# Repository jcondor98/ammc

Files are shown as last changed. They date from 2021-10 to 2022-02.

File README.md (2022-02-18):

# Bachelor degree thesis

This branch contains the LaTeX source code and compiled PDFs for my bachelor
degree thesis and slides for the AVR Multi Motor Control project presentation.

**Relator**: Prof. Giorgio Grisetti
**Correlator**: Docs. Barbara Bazzana
**Evaluator**: Profs. Silvia Bonomi

The thesis is presented in the degree session of _March 2022_.

# Building

### Requirements
All the LaTeX source code in this branch can be compiled using the _GNU Make_
build system.

Building the thesis requires `xelatex` and `bibtex`.

Building the presentation slides requires `xelatex`.

A full _TeXLive_ installation is recommended.

### GNU Make recipes

**Command** | **Description**
:-:|---
`make thesis`       | Builds the thesis PDF with `xelatex`
`make bibliography` | Builds the bibliography with `bibtex`
`make slides`       | Builds the presentation slides with `xelatex`
`make`              | Alias for `make thesis`
`make clean`        | Removes all the build auxiliary files

For a complete thesis build (with correct references and bibliography), run the
following commands:

```
make thesis
make bibliography
make thesis
make thesis
```

### Target files
The thesis can be found under the main directory of this branch as `thesis.pdf`

The presentation slides can be found under the `presentation/` directory as
`slides.pdf`

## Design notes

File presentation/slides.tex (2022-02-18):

% AVR Multi Motor Control - Paolo Lucchesi
% Slides for project presentation
\documentclass{beamer}
\usepackage[T1]{fontenc}
\usepackage[utf8]{inputenc}
\usepackage{longtable,booktabs,array}
\usepackage{caption}
\usepackage{adjustbox}
\usepackage{palatino}

\newcommand*{\LimitedIncludeGraphics}[2][]{%
\begin{adjustbox}{max size={\textwidth}{\textheight}}
    %
\end{adjustbox}
}

\usetheme[]{Berlin}
\usecolortheme{beaver}
\beamertemplatenavigationsymbolsempty

\hypersetup{
  pdfauthor={Paolo Lucchesi},
  hidelinks
}

\title{AVR Multi Motor Control}
\author{Paolo Lucchesi}
\date{}

\begin{document}
\frame{\titlepage}

\hypertarget{introduction}{%
\section{Introduction}\label{introduction}}

\begin{frame}{What is ammc?}
\emph{AVR Multi Motor Control} is an electrical motor management
hardware/software ecosystem composed of:

\begin{itemize}
  \item A text-based \textbf{client} application
  \item One \textbf{master} controller
  \item One or more \textbf{slave} controllers
\end{itemize}
\end{frame}

\begin{frame}{Features}
\begin{itemize}
  \item Text-based client application for POSIX environments
  \item Master and Slave(s) controller firmware
  \item Fully binary Client-Master communication protocol on top of the serial
    interface
  \item Fully binary Master-Slave communication protocol on top of the I2C
    interface
  \item Up to 126 DC motors (limited by 7-bit I2C Slave addressing, 0x00 is
    reserved)
  \item Ability to get and set the DC motors speed, individually
  \item Software defined PID controller embedded in each Slave controller
\end{itemize}
\end{frame}

\begin{frame}{Development}
\begin{itemize}
  \item Focus on \textbf{modularity}
  \item Keeping \emph{SOLID} principles in mind
  \begin{itemize}
    \item Extensibility through the Open-Close Principle
    \item Attention on module call directions following the Single
      Responsability Principle
  \end{itemize}
  \item Exhaustive \textbf{documentation} on multiple depths
  \begin{itemize}
    \item README.md file in the git repository
    \item Source code documentation generated with \emph{doxygen}
    \item Client application's man page
    \item Bachelor degree thesis
  \end{itemize}
  \item GNU Make build system
  \item Absence of third-party non-standard libraries
\end{itemize}
\end{frame}

\hypertarget{client-application}{%
\section{Client Application}\label{client-application}}

\begin{frame}{Features}
\begin{itemize}
  \item Granular handling for getting and setting motors' speed
  \item Terminal User Interface implemented as a command shell
  \item Support for non-interactive use (i.e.~scripting)
  \item Communication with master controller using the serial protocol
  \item Compatible with POSIX-compliant environments
  \item Comes with a man page
\end{itemize}
\end{frame}

\begin{frame}{Software modules}
\begin{figure}
  \centering
  \LimitedIncludeGraphics{../source/images/client-deps.png}
  \caption{Client application modules dependency graph}
\end{figure}
\end{frame}

\begin{frame}{User Interface}
External commands allow to interface the master controller:

\begin{itemize}
  \item \texttt{connect\ \textless{}device-path\textgreater{}}
  \item \texttt{ping\ \textless{}motor-id\textgreater{}}
  \item \texttt{get-speed\ \textless{}motor-id\textgreater{}}
  \item \texttt{set-speed\ \textless{}motor-id\textgreater{}=\textless{}speed\textgreater{}}
  \item \texttt{apply}
  \item \texttt{set-slave-addr}
\end{itemize}
\end{frame}

\hypertarget{master-controller}{%
\section{Master Controller}\label{master-controller}}

\begin{frame}{Features}
\begin{itemize}
  \item Is itself an \textbf{ATMega2560} microcontroller unit
  \item Interfaces the client applications with the slave controllers
  \item Communicates with the client via serial
  \item Communicates with slaves via I2C
  \item Interrupt-driven communication
  \item Comes with a power saving policy
\end{itemize}
\end{frame}

\begin{frame}{Hardware setup}
\begin{figure}
  \centering
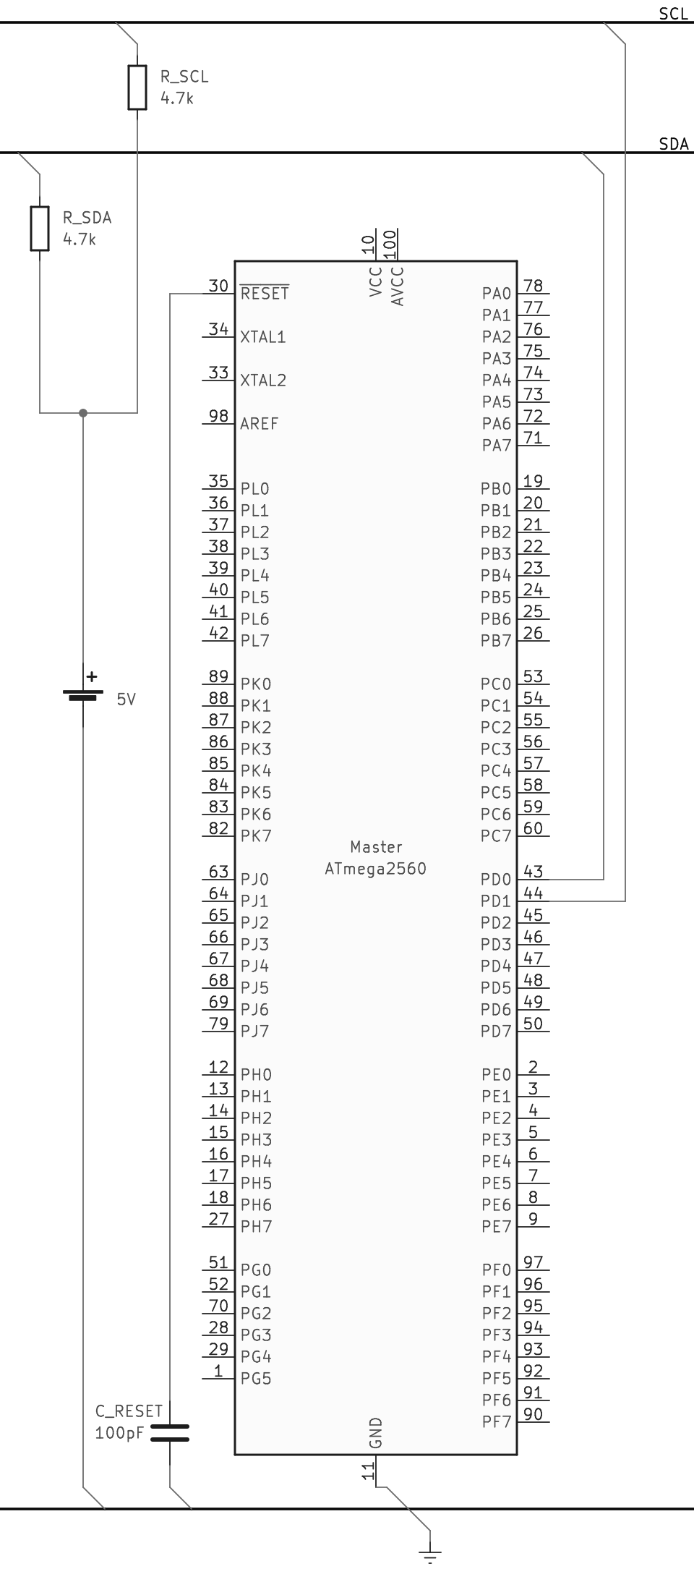
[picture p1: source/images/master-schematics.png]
  
  \caption{Master controller schematics}
\end{figure}
\end{frame}

\begin{frame}{Software modules}
\begin{figure}
  \centering
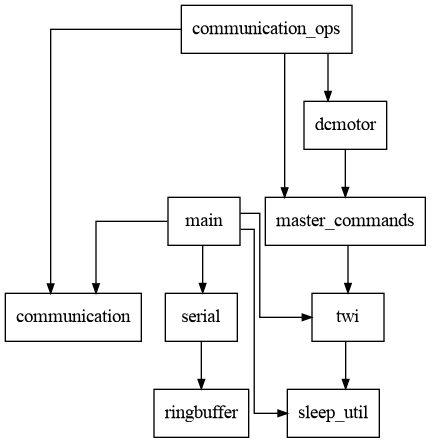
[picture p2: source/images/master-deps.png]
  
  \caption{Master controller firmware modules dependency graph}
\end{figure}
\end{frame}

\hypertarget{slave-controller}{%
\section{Slave Controller}\label{slave-controller}}

\begin{frame}{Features}
\begin{itemize}
  \item Is itself an \textbf{ATMega2560} microcontroller unit
  \item Manages a single dc motor
  \item Communicates with the master controller using the \textbf{I2C}
    interface
  \item Execute commands issued by the master controller
  \item Embedded software-defined \textbf{Proportional-Integral-Derivative}
    controller
\end{itemize}
\end{frame}

\begin{frame}{Hardware setup}
\begin{figure}
  \centering
  \LimitedIncludeGraphics{../source/images/slave-schematics.png}
  \caption{Slave controller schematics}
\end{figure}
\end{frame}

\begin{frame}{Software modules}
\begin{figure}
  \centering
  \LimitedIncludeGraphics{../source/images/slave-deps.png}
  \caption{Slave controller firmware modules dependency graph}
\end{figure}
\end{frame}

\hypertarget{client-master-communication}{%
\section{Client-Master
Communication}\label{client-master-communication}}

\begin{frame}{Characteristics}
\begin{itemize}
  \item Built on top of the \textbf{serial} interface
  \item Completely binary
  \item \textbf{Packet}-based
  \item Packet integrity is checked via \textbf{CRC-8} checksum
  \item Interrupt-driven for the master controller
\end{itemize}
\end{frame}

\begin{frame}{Packets}
Each packet is composed of:

\begin{itemize}
  \item A \textbf{header} containing:
  \begin{itemize}
    \item Packet id
    \item Packet type
    \item Whole packet size
    \item DC motor selector
  \end{itemize}
  \item An eventual \textbf{body}
  \item A trailing CRC-8 \textbf{checksum}
\end{itemize}
\end{frame}

\begin{frame}{Packet types}
\begin{longtable}[]{@{}cc@{}}
\toprule
  Type & Actual value \\
\midrule
\endhead
  \texttt{COM\_TYPE\_NULL} & \texttt{0x00} \\
  \texttt{COM\_TYPE\_HND} & \texttt{0x01} \\
  \texttt{COM\_TYPE\_ACK} & \texttt{0x02} \\
  \texttt{COM\_TYPE\_NAK} & \texttt{0x03} \\
  \texttt{COM\_TYPE\_ECHO} & \texttt{0x04} \\
  \texttt{COM\_TYPE\_PING} & \texttt{0x05} \\
  \texttt{COM\_TYPE\_GET\_SPEED} & \texttt{0x06} \\
  \texttt{COM\_TYPE\_SET\_SPEED} & \texttt{0x07} \\
  \texttt{COM\_TYPE\_APPLY} & \texttt{0x08} \\
  \texttt{COM\_TYPE\_DAT} & \texttt{0x09} \\
  \texttt{COM\_TYPE\_SET\_ADDR} & \texttt{0x0A} \\
  \texttt{COM\_TYPE\_LIMIT} & \texttt{0x0B} \\
\bottomrule
\end{longtable}
\end{frame}

\hypertarget{i2c-communication}{%
\section{I2C Communication}\label{i2c-communication}}

\begin{frame}{Features}
\begin{itemize}
  \item Master-Slave architecture
  \item Completely binary
  \item \textbf{Interrupt-driven} for both master and slaves
  \item \textbf{Broadcasting} capabilities through the \emph{general-call
    address} \texttt{0x00}
  \item Follows the original Philips I2C specification (year 2000)
\end{itemize}
\end{frame}

\begin{frame}{Communication Frames}
The communication frames is composed of two parts:

\begin{itemize}
  \item A heading byte representing the master \textbf{command}
  \item An optional command \textbf{argument}
\end{itemize}

\begin{longtable}[]{@{}cc@{}}
\toprule
  Command & Code \\
\midrule
\endhead
  \texttt{CMD\_GET} & \texttt{0x00} \\
  \texttt{CMD\_SET} & \texttt{0x01} \\
  \texttt{CMD\_APPLY} & \texttt{0x02} \\
  \texttt{CMD\_PING} & \texttt{0x03} \\
  \texttt{CMD\_SET\_ADDR} & \texttt{0x04} \\
\bottomrule
\end{longtable}
\end{frame}

\end{document}

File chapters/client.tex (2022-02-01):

\chapter{Client-side user interaction}
\label{ch:client}
A client program has been realized to manipulate the dc motors directly from
the PC. It can get and set the speed of individual motors, and to apply all the
previously set speeds for all of them at once.\\ A brief list of the client's
features is given below:
\begin{itemize}
  \item Granular handling for getting and setting motors' speed
  \item Modular and extensible software architecture
  \item Terminal User Interface, implemented as a command shell
  \item Support for non-interactive use (i.e.\ scripting)
  \item Communication with master controller using the serial protocol
  \item Compatible with POSIX-compliant environments
\end{itemize}
The client is also documented with a man page, which can be found in section
\ref{sec:client-manpage}.

\section{User Interface}
The end user interacts with the whole ammc ecosystem using a text-based client.
It consists in a shell module, which I had written myself, offering some
\emph{internal commands} (hardcoded in the shell module itself) and is extended
by \emph{external commands} (found in a separated source code entity, and that
can even be compiled in a detached transaction unit).

A particular focus was made on the software architecture: indeed, every
external command can be realized standalone, and it is easy to add new
commands just by altering the \texttt{client/source/shell\_commands.c} source
file.

\section{Primitives offered}
The commands that can be used to interface with the ammc ecosystem are the
following:
\begin{description}
  \item[connect <device-path>] Connect to a master controller, given the path
    to the block device representing it.
  \item[get-speed <motor-id>] Get the speed of a dc motor given its id.
    The motor id must be specified as a decimal number.
  \item[set-speed <motor-id>=<speed>] Set the speed of a dc motor given its id.
    The motor id must be specified as a decimal number and the speed must be
    specified in rpm.
  \item[apply] Apply the previously set speed for all the dc motors.
  \item[set-slave-addr] Set a new TWI address for a slave controller.
\end{description}

\subsection{Non-interactive mode}
The client shell is capable of running in non-interactive (i.e.\ scripting)
mode with the \texttt{-s} option.  If so, it will parse the input from a
specified text file, or from \texttt{stdin} if not provided.  A shell launched
in non-interactive mode will not print shell prompts, and exit when end-of-file
is encountered or on command failure.

\section{Serial module}
The client's serial module has been realized using the POSIX \emph{termios}
interface. Unlike the master controller's counterpart, all its code is
reentrant, therefore multiple instances of multiple serial devices can
theoretically exist at the same time.

From the client's perspective, the master controller is seen as a file
descriptor, and the end user just have to specify the path of the block device
file representing the serial communication channel (e.g. \texttt{/dev/ttyACM0})
using the \texttt{connect} command.

\section{Specification}

\subsection{Software modules}
An exhaustive list of software modules for the client application is given
in table \ref{tab:client-spec-modules}. File paths are relative to the
\texttt{client/} directory.

\begin{table}[h!]
  \begin{tabularx}{\textwidth}{c X X}
    \toprule
    Module & Description & Files \\
    \midrule
    communication &
      Top-level communication routines &
      \texttt{include/communication.h},
      \texttt{source/communication.c} \\
    crc &
      CRC generation and checking routines &
      \texttt{include/crc.h},
      \texttt{source/crc.c} \\
    debug &
      Debug facilities &
      \texttt{include/debug.h} \\
    main &
      Main client application routine &
      \texttt{source/main.c} \\
    packet &
      Packet generation and manipulation routines &
      \texttt{include/packet.h},
      \texttt{source/packet.c} \\
    ringbuffer &
      Circular buffer data structure &
      \texttt{include/ringbuffer.h},
      \texttt{source/ringbuffer.c} \\
    serial &
      Serial communication layer &
      \texttt{include/serial.h},
      \texttt{source/serial.c} \\
    shell &
      Main program shell with built-in commands &
      \texttt{include/shell.h},
      \texttt{source/shell.c} \\
    shell\_commands &
      External commands to interact with the master controller &
      \texttt{source/shell\_commands.c} \\
    \bottomrule
  \end{tabularx}
  \caption{Client application software modules}
  \label{tab:client-spec-modules}
\end{table}

\subsection{Modules dependency graph}
The dependency graph for the client application software modules is shown in
figure \ref{img:client-deps-graph}. The \emph{debug} module is excluded. Notice
how the dependency flow goes in one direction (from top to bottom); this is the
result of the software architecture policy used.
\begin{figure}[hbp]
\begin{centering}
  
  \caption{Client application modules dependency graph}
  \label{img:client-deps-graph}
\end{centering}
\end{figure}

\section{Man page}
\label{sec:client-manpage}
{
  \ttfamily
  \import{./misc/}{manpage.tex}
}

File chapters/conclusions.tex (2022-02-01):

\chapter{Conclusions}
\label{ch:conclusions}
In this work I developed an electrical motor handling hardware/software
solution with modularity and extensibility in mind. In this very final chapter
I demonstrate how ammc can be used in practice and I explain how it could be
developed further in the future.

\section{Example setup}

\subsection{Hardware}
The hardware required for the example setup given here is the following:
\begin{itemize}
  \item One \emph{ATMega2560} microcontroller unit for the master controller
  \item One \emph{ATMega2560} microcontroller unit for the slave controller
  \item One dc motor with embedded two-phase encoder
  \item Two $4.7 k\Omega$ resistors for the I2C open-drain
  \item One capacitor of about $100 pF$ to inhibit the reset-over-serial
    capabilities of the ATMega2560 board
  \item One h-bridge driver consistent with the dc motor voltage and power
    requirements (e.g.\ $12 V,\ 2 A$)
  \item A power supply compatible with the h-bridge and motor voltage and
    power requirements (e.g.\ $12 V,\ 24 W$)
\end{itemize}

The hardware setup must be performed as shown in figures \ref{img:master-sch}
and \ref{img:slave-sch}.
The motor must be powered consistently with its requirements. The AVR
microcontrollers can be powered using their USB sockets. The I2C reference
voltage can be set by using a $5 V$ output pin of the master controller board.

\subsection{Software}
The software can be built and eventually flashed using GNU Make. the
\emph{avr-gcc} toolchain and the \emph{avr-libc} library are required for the
build, while \emph{avrdude} is required for flashing.

The \texttt{make} command will build all the ammc software, i.e.\ the master
and slave controllers firmwares and the client application. The \texttt{make
master-flash} and the \texttt{make slave-flash} commands will flash the master
and slave firmwares into their respective microcontrollers.

At last, the user may want to use the \texttt{set-slave-addr} command to assign
an arbitrary address to the only slave controller.

\section{Future work}

\subsection{Extended connectivity}
The extension of the master controller connectivity would make ammc suitable
for whole new range of application possibilities. For example, \emph{LoRaWAN}
and similar communication vectors would make ammc a motor management system
suitable for dc motor distributed in a wide-area. The use of multiple wired
low-level communication means such as SPI or raw serial ports would make ammc
suitable for a multi-master, multi-group setup.

\subsection{Programming API}
The client application offers a non-interactive mode for basic scriping
functionality. Thus it is good for basic automation, it is quite limited when
more complex features are required, such as an advanced use of logic or control
flow capabilities. For this purpose, the implementation of a programming API,
eventually with bindings in various languages, would make the ammc
functionality directly available to the programmer as high-level functions.

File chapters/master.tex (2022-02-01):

\chapter{Master controller}
\label{ch:master}
The master controller handles all the slave controllers, dispaching arbitrary
commands to them using the I2C protocol. It also communicates directly with the
client application via serial port.

\section{Hardware setup}
The master controller itself is an AVR \emph{ATMega2560} microcontroller
unit\cite{at2560-ref}. This particular MCU has features convenient for this
project, such as:
\begin{itemize}
  \item I2C dedicated hardware subsystem
  \item Serial-over-USB bridge
  \item Relatively powerful specifications for future feature adding
  \item Plenty of timers and outgoing power pins
\end{itemize}

A $100 pF$ capacitor is used to block the reset capabilities of the
serial-over-usb controller and enhance the serial channel reliability. Two
$4.7 k\Omega$ resistors are used as open-drain resistors for the I2C bus.

\section{I2C setup}
The I2C protocol is used to communicate with slave controllers. Transmission
and reception are interrupt-based, and no busy-wait is used.

The I2C module has broadcasting capabilities, according to the informations
found in the I2C standard I2C standard\cite{i2c-ref}; the broadcasting (i.e.\
\emph{general call}) address used is \texttt{0x00}. As stated by the standard,
the master controller has no knowledge on the number or identity of the slaves
receiving a broadcast frame.

\section{Power management}
An own-written wrapper for the avr-gcc standard library's sleep functionalities
is used for power management.  By default, the master controller is in
\emph{idle} mode, and it is awakened by any raised interrupt, e.g.\ by incoming
serial or I2C data; then, its main loop routine is executed and, if no other
operations must be performed, it returns in idle mode.

The master controller is also put in idle when waiting for data inside serial
or I2C routines; this is possible thanks to the interrupt-driven nature of the
aforementioned modules.

\section{Specification}

\subsection{Software modules}
An exhaustive list of software modules for the master controller firmware is
given in table \ref{tab:master-spec-modules}. File paths are relative to the
\texttt{master/} directory.

\begin{table}[bth]
  \begin{tabularx}{\textwidth}{c X X}
    \toprule
    Module & Description & Files \\
    \midrule
    communication &
      Top-level communication routines &
      \texttt{include/communication.h},
      \texttt{source/communication.c} \\
    communication\_ops &
      Application-specific use cases &
      \texttt{source/communication\_ops.c} \\
    crc &
      CRC generation and checking routines &
      \texttt{include/crc.h},
      \texttt{source/crc.c} \\
    dcmotor &
      Top-level routines for interfacing slave controllers &
      \texttt{include/dcmotor.h},
      \texttt{source/dcmotor.c} \\
    main &
      Main and power management routines &
      \texttt{source/main.c} \\
    master\_commands &
      Interface to issue commands to slave controllers &
      \texttt{source/master\_commands.c},
      \texttt{include/master\_commands.h} \\
    packet &
      Packet generation and manipulation routines &
      \texttt{include/packet.h},
      \texttt{source/packet.c} \\
    ringbuffer &
      Circular buffer data structure &
      \texttt{include/ringbuffer.h},
      \texttt{source/ringbuffer.c} \\
    serial &
      Serial communication layer &
      \texttt{include/serial.h},
      \texttt{source/serial.c} \\
    sleep\_util &
      Wrapper for the avr-libc power management facilities &
      \texttt{include/sleep\_util.h} \\
    twi &
      I2C/TWI communication layer &
      \texttt{include/twi.h},
      \texttt{source/twi.c} \\
    \bottomrule
  \end{tabularx}
  \caption{Master application software modules}
  \label{tab:master-spec-modules}
\end{table}

\subsection{Modules dependency graph}
The dependency graph for the master controller's software modules is shown in
figure \ref{img:master-deps-graph}. The \emph{debug} module is excluded. Notice
how the dependency flow goes in one direction (from top to bottom); this is the
result of the software architecture policy used.
\begin{figure}[hbt]
\begin{centering}
  
  \caption{Master controller modules dependency graph}
  \label{img:master-deps-graph}
\end{centering}
\end{figure}

\subsection{Circuit schematics}
The complete circuit schematics for the master controller and all its
components is shown in figure \ref{img:master-sch}.
\begin{figure}[hbp]
\begin{centering}
  
  \caption{Master controller schematics}
  \label{img:master-sch}
\end{centering}
\end{figure}

\subsection{Wiring}
The wiring correspondence for the master controller MCU is shown in table
\ref{tab:master-wiring}.
\begin{table}[hb]
  \begin{tabularx}{\textwidth}{c l X}
    \toprule
    Board pin & MCU pin & Description \\
    \midrule
    D20   & 44/PD1/INT1/SDA & I2C data bus \\
    D21   & 43/PD0/INT0/SCL & I2C clock bus \\
    RESET & RESET           & On-board MCU reset pin \\
    \bottomrule
  \end{tabularx}
  \caption{Master controller wiring}
  \label{tab:master-wiring}
\end{table}

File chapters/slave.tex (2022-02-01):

\chapter{Slave controllers}
\label{ch:slave}
Each slave controller directly handles a single dc motor, receiving commands
from the master controller via I2C. It must offer an interface to get and
manipulate its motor's speed.

The slave controller produces a PWM wave having a duty cycle consistent with
the speed (given in RPM) specified by the end user in order to control its
motor.

Furthermore, it comes with a software Proportional-Integral-Derivative
controller to correct the bias between target and actual motor speeds.

\section{Hardware setup}
The slave controller itself is an AVR \emph{ATMega2560} microcontroller
unit\cite{at328p-ref}, which offers the following features of interest:

\begin{itemize}
  \item Dedicated I2C hardware subsystem
  \item PWM-capable 8-bit and 16-bit timers
\end{itemize}

Apart from the motor itself (along with its power supply and its dedicated
H-bridge control board) no additional hardware is used.

\section{I2C setup}
A slave controller communicates with the master controller using the I2C
protocol. As for the master controller, both transmission and reception are
interrupt-based.

The slave controller is always passive on the bus, waiting to be addressed by
the master.

\subsection{Dynamic I2C addressing}
Each slave controller needs a unique I2C address. Basically, there are two ways
to assign an arbitrary address to a slave.

The first and most trivial one is to define the \texttt{TW\_DEFAULT\_ADDR}
macro to the desired address when building the slave controller firmware. This
solution is impractical for obvious reasons and should be avoided.

The second method is to connect the master and slave controllers via I2C and
the master controller with the client via serial. Then the
\texttt{set-slave-addr} command can be used to change the I2C address to the
desired one. The changes take place immediately, as the slave controller's I2C
software module is reinitialized, and they will be saved in the EEPROM embedded
into the AVR microcontroller for durability.

\section{Proportional-Integral-Derivative controller}
An own-written, software-defined Proportional-Integral-Derivative controller is
used to correct the actual motor speed. As for any PID device, the equation
controlling the error is:
\begin{equation}
  u(t) = K_p e(t) + K_i \int_{t_0}^t e(\tau)\,d\tau + K_d \frac{d}{dt}\,e(t)
\end{equation}
being:
\begin{itemize}
  \item $u(t)$ the PID control variable
  \item $K_p$ the proportional gain
  \item $K_i$ the integral gain
  \item $K_d$ the derivative gain
  \item $e(t)$ the measured speed error
\end{itemize}

\subsection{Measuring speed}
For actual PID capabilities, the slave controller must sample the actual speed
of the dc motor at fixed intervals. Therefore, the motor must have an embedded,
two-phase digital encoder.

In fact, one phase is wired to an interrupt-enabled input pin, so the slave
controller is notified immediately when an encoder signal (raising edge) is
generated. Every sampling intervals, the PID routine takes the motor's actual
position (measured by the cumulative number of encoder triggers) and computes
its real speed.

\subsection{Approximations}
Of course, a software digital PID controller can not compute exact integrals
and derivatives, so it is necessary to use approximation.

The integral operation is approximated using \emph{Riemann sums}. Given a time
delta $\Delta t$ (the actual speed sampling interval in this particular case),
the approximating law is defined as:
\begin{equation}
  \int_{t_0}^t e(\tau)\,d\tau \approx \sum_{k=1}^n e(t_k^*) \cdot \Delta t
\end{equation}
The derivative operation is approximated using its
definition\cite{levy-num-analysis}:
\begin{equation}
  \frac{d}{dt}\,e(t) = \lim_{\Delta t \to 0} \frac{e(t + \Delta t) - e(t)}{\Delta t} \implies
  \frac{d}{dt}\,e(t) \approx \frac{e(t + \Delta t) - e(t)}{\Delta t}
\end{equation}
being $\Delta t$ a time delta (again, the actual speed sampling interval).

\section{Power management}
The same avr-libc wrapper written for the master controller power management is
used.
By default, the slave controller is in \emph{idle} mode, and it is awakened by
any raised interrupt. The main loop routine is executed and the idle mode is
entered again. Like for the master controller, the slave is put in idle when
waiting for the I2C routines to return.

The AVR idle mode allows the timers to work, so the slave controller can
generate PWM waves to control the motors, even while sleeping.

\section{Specification}

\subsection{Software modules}
An exhaustive list of software modules for the slave controllers firmware is
given in table \ref{tab:slave-spec-modules}. File paths are relative to the
\texttt{slave/} directory.

\begin{table}[ht]
  \begin{tabularx}{\textwidth}{c X X}
    \toprule
    Module & Description & Files \\
    \midrule
    command &
      Interface to handle commands issued by the master controller &
      \texttt{source/command.c},
      \texttt{include/command.h} \\
    dcmotor &
      High-level interface to the dc motor &
      \texttt{source/dcmotor.c},
      \texttt{include/dcmotor.h} \\
    dcmotor\_phy &
      HAL interface for direct (i.e.\ physical) dc motor handling &
      \texttt{source/dcmotor\_phy.c},
      \texttt{include/dcmotor\_phy.h},
      \texttt{include/dcmotor\_phy\_params.h} \\
    dcmotor\_pid &
      PID controller routines &
      \texttt{source/dcmotor\_pid.c},
      \texttt{include/dcmotor\_pid.h} \\
    main &
      Main and power management routines &
      \texttt{source/main.c} \\
    sleep\_util &
      Wrapper for the avr-libc power management facilities &
      \texttt{include/sleep\_util.h} \\
    twi &
      I2C/TWI communication layer &
      \texttt{include/twi.h},
      \texttt{source/twi.c} \\
    \bottomrule
  \end{tabularx}
  \caption{Slave application software modules}
  \label{tab:slave-spec-modules}
\end{table}

\subsection{Modules dependency graph}
The dependency graph for the slave controllers' software modules is shown in
figure \ref{img:slave-deps-graph}. The \emph{debug} module is excluded.
\begin{figure}[ht]
\begin{centering}
  
  \caption{Slave controller modules dependency graph}
  \label{img:slave-deps-graph}
\end{centering}
\end{figure}

\subsection{Circuit schematics}
The complete circuit schematics for the slave controller and all its components
is shown in figure \ref{img:slave-sch}. This circuit can be repeated multiple
times (up to 126) in a single ammc ecosystem.
\begin{figure}[htb]
\begin{centering}
  
  \caption{Slave controller schematics}
  \label{img:slave-sch}
\end{centering}
\end{figure}

\subsection{Wiring}
The wiring correspondence for the slave controller MCU is shown in table
\ref{tab:slave-wiring}.
\begin{table}[htb]
  \begin{tabularx}{\textwidth}{c l X}
    \toprule
    Board pin & MCU pin & Description \\
    \midrule
    D20 & 44/PD1/INT1/SDA    & I2C data bus \\
    D21 & 43/PD0/INT0/SCL    & I2C clock bus \\
    D13 & 26/PB7/OC0A/PCINT7 & Forward PWM output to the dc motor \\
    D13 & 1/PG5/OC0B         & Forward PWM output to the dc motor \\
    D53 & 19/PB0/PCINT0      & Encoder phase A, interrupt-enabled \\
    D52 & 20/PB1/PCINT1      & Encoder phase B \\
    \bottomrule
  \end{tabularx}
  \caption{Slave controller wiring}
  \label{tab:slave-wiring}
\end{table}

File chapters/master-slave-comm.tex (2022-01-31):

\chapter{Master-Slave communication}
\label{ch:master-slave-comm}
The master and slave controllers communicate to each other using the I2C
bus. Naturally, the master controller is responsible for starting communication
sessions, addressing one or all the slaves.

The bitrate is set to 100kbit/s, i.e.\ the maximum speed available for the
original I2C standard\cite{i2c-ref} (excluding fast modes, which were
implemented later).

\subsection{Hardware setup}
The I2C bus itself is a pair of bus rails, named \texttt{SDA} and \texttt{SCL},
representing data and bus clock respectively.

Two $4.7 k\Omega$ resistors connects \texttt{SDA} and \texttt{SCL} to a $5V$
voltage generator and act as \emph{open-drain} resistors.
% TODO: Footnote?

\subsection{Communication frames}
The first byte of the I2C communication frame (excluding, of course, the slave
address) is an 8-bit unsigned integer representing the command sent by the
master to the slave. The trailing data represents an argument, with its size
and shape depending on the type of command issued. Command codes, with their
specific arguments, are shown in table \ref{tab:i2c-commands}.

\begin{table}[bh]
  \begin{tabularx}{\textwidth}{c c c X}
    \toprule
    Command & Code & Arg.\ size (bytes) & Description \\
    \midrule
      \texttt{CMD\_GET}       & \texttt{0x00} & - & Get the dc motor speed in rpm \\
      \texttt{CMD\_SET}       & \texttt{0x01} & 1 & Set the dc motor target speed \\
      \texttt{CMD\_APPLY}     & \texttt{0x02} & - & Apply the previously set target speed \\
      \texttt{CMD\_ECHO}      & \texttt{0x03} & 1 & Send back the received character to the master (debug)\\
      \texttt{CMD\_SET\_ADDR} & \texttt{0x04} & 1 & Set a different I2C slave address \\
    \bottomrule
  \end{tabularx}
  \caption{Master-to-slave commands}
  \label{tab:i2c-commands}
\end{table}

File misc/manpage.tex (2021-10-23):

\subsection*{NAME}
\textbf{ammc} — AVR Temperature Monitor client

\subsection*{SYNOPSIS}
\textbf{ammc} [\textbf{-s} \emph{[script]}] [\textbf{-c} \emph{device-file}] \\
\textbf{ammc} -h

\subsection*{DESCRIPTION}
\textbf{ammc} is a multi-motor control device realized with an AVR microcontroller;
this program is an ad-hoc, tui client to interface it.  
The ammc device is designed to work with DC motors with an embedded or external
encoder.

\subsubsection*{Options}
\begin{description}
\item[-c \emph{device-file}]
\ \ Connect to the device identified by \emph{device-file} (e.g. /dev/ttyACM0)

\item[-s \emph{[script]}]
\ \ Execute in script mode (do not print prompt, exit on error etc...), being
\ \ \emph{script} a file containing a command each line. If \emph{script} is not given,
\ \ standard input is used

\item[-h]
\ \ Display a help message and exit
\end{description}

\subsubsection*{Commands}
\begin{description}
  \item[\textbf{help} [\emph{command}\textrm{]}]
  \ \ Show help, also for a specific command if an argument is given

  \item[\textbf{connect} <\emph{device\_path}>]
  \ \ Connect to an ammc Master MCU given its device file (usually under /dev)

  \item[\textbf{disconnect}]
  \ \ Close an existing connection - Has no effect on the device

  \item[\textbf{dev-echo} <\emph{arg}> [\emph{arg2} \emph{arg3} \emph{...}\textrm{]}]
  \ \ Send a string to the device, which should send it back

  \item[\textbf{get-speed} <\emph{motor-id}>]
  \ \ Get the speed of a DC motor in RPM

  \item[\textbf{set-speed} <\emph{motor-id}>=<\emph{value}>]
  \ \ Set the speed of a DC motor in RPM
\end{description}

\subsection*{AUTHOR}
Paolo Lucchesi <paololucchesi@protonmail.com> \\
https://www.github.com/jcondor98/ammc

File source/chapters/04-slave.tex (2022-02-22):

\chapter{Slave controllers}
\label{ch:slave}
Each slave controller directly handles a single dc motor, receiving commands
from the master controller via I2C. It must offer an interface to get and
manipulate its motor's speed.

The slave controller produces a PWM wave having a duty cycle consistent with
the speed (given in RPM) specified by the end user in order to control its
motor.

Furthermore, it comes with a software Proportional-Integral-Derivative
controller to correct the bias between target and actual motor speeds.

\section{Hardware setup}
The slave controller itself is an AVR \emph{ATMega2560} microcontroller
unit\cite{at2560-ref}, which offers the following features of interest:

\begin{itemize}
  \item Dedicated I2C hardware subsystem
  \item PWM-capable 8-bit and 16-bit timers
\end{itemize}

Apart from the motor itself (along with its power supply and its dedicated
H-bridge control board) no additional hardware is used.

\section{I2C setup}
A slave controller communicates with the master controller using the I2C
protocol. As for the master controller, both transmission and reception are
interrupt-based.

The slave controller is always passive on the bus, waiting to be addressed by
the master.

\subsection{Dynamic I2C addressing}
Each slave controller needs a unique I2C address. Basically, there are two ways
to assign an arbitrary address to a slave.

The first and most trivial one is to define the \texttt{TW\_DEFAULT\_ADDR}
macro to the desired address when building the slave controller firmware. This
solution is impractical for obvious reasons and should be avoided.

The second method is to connect the master and slave controllers via I2C and
the master controller with the client via serial. Then the
\texttt{set-slave-addr} command can be used to change the I2C address to the
desired one. The changes take place immediately, as the slave controller's I2C
software module is reinitialized, and they will be saved in the EEPROM embedded
into the AVR microcontroller for durability.

\section{Proportional-Integral-Derivative controller}
An own-written, software-defined Proportional-Integral-Derivative controller is
used to correct the actual motor speed. As for any PID device, the equation
controlling the error is:
\begin{equation}
  u(t) = K_p e(t) + K_i \int_{t_0}^t e(\tau)\,d\tau + K_d \frac{d}{dt}\,e(t)
\end{equation}
being:
\begin{itemize}
  \item $e(t)$ the measured speed error
  \item $u(t)$ the PID control variable
  \item $K_p$ the proportional gain
  \item $K_i$ the integral gain
  \item $K_d$ the derivative gain
\end{itemize}

\subsection{Measuring speed}
For actual PID capabilities, the slave controller must sample the actual speed
of the dc motor at fixed intervals. Therefore, the motor must have an embedded,
two-phase digital encoder.

In fact, one phase is wired to an interrupt-enabled input pin, so the slave
controller is notified immediately when an encoder signal (raising edge) is
generated. Every sampling interval, the PID routine takes the motor's actual
position (measured by the cumulative number of encoder triggers) and computes
its real speed.

\subsection{Approximations}
Of course, a software digital PID controller can not compute exact integrals
and derivatives, so it is necessary to use approximation.

The integral operation is approximated using \emph{Riemann sums}. Given a time
delta $\Delta t$ (the actual speed sampling interval in this particular case),
the approximating law is defined as:
\begin{equation}
  \int_{t_0}^t e(\tau)\,d\tau \approx \sum_{k=1}^n e(t_k^*) \cdot \Delta t
\end{equation}
The derivative operation is approximated using its
definition\cite{levy-num-analysis}:
\begin{equation}
  \frac{d}{dt}\,e(t) = \lim_{\Delta t \to 0} \frac{e(t + \Delta t) - e(t)}{\Delta t} \implies
  \frac{d}{dt}\,e(t) \approx \frac{e(t + \Delta t) - e(t)}{\Delta t}
\end{equation}
being $\Delta t$ a time delta (again, the actual speed sampling interval).

%\subsection{PID parameters}
% TODO

\section{Power management}
The same avr-libc wrapper written for the master controller power management is
used.
By default, the slave controller is in \emph{idle} mode, and it is awakened by
any raised interrupt. The main loop routine is executed and the idle mode is
entered again. Like for the master controller, the slave is put in idle when
waiting for the I2C routines to return.

The AVR idle mode allows the timers to work, so the slave controller can
generate PWM waves to control the motors, even while sleeping.

\section{Specification}

\subsection{Software modules}
An exhaustive list of software modules for the slave controllers firmware is
given in table \ref{tab:slave-spec-modules}. File paths are relative to the
\texttt{slave/} directory.

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

\subsection{Modules dependency graph}
The dependency graph for the slave controllers' software modules is shown in
figure \ref{img:slave-deps-graph}. The \emph{debug} module is excluded.
\begin{figure}[ht]
\begin{centering}
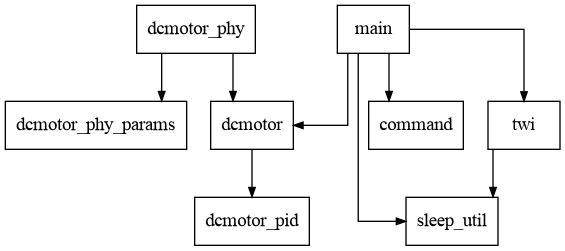
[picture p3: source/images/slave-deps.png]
  
  \caption{Slave controller modules dependency graph}
  \label{img:slave-deps-graph}
\end{centering}
\end{figure}

\subsection{Circuit schematics}
The complete circuit schematics for the slave controller and all its components
is shown in figure \ref{img:slave-sch}. This circuit can be repeated multiple
times (up to 126) in a single ammc ecosystem.
\begin{figure}[htb]
\begin{centering}
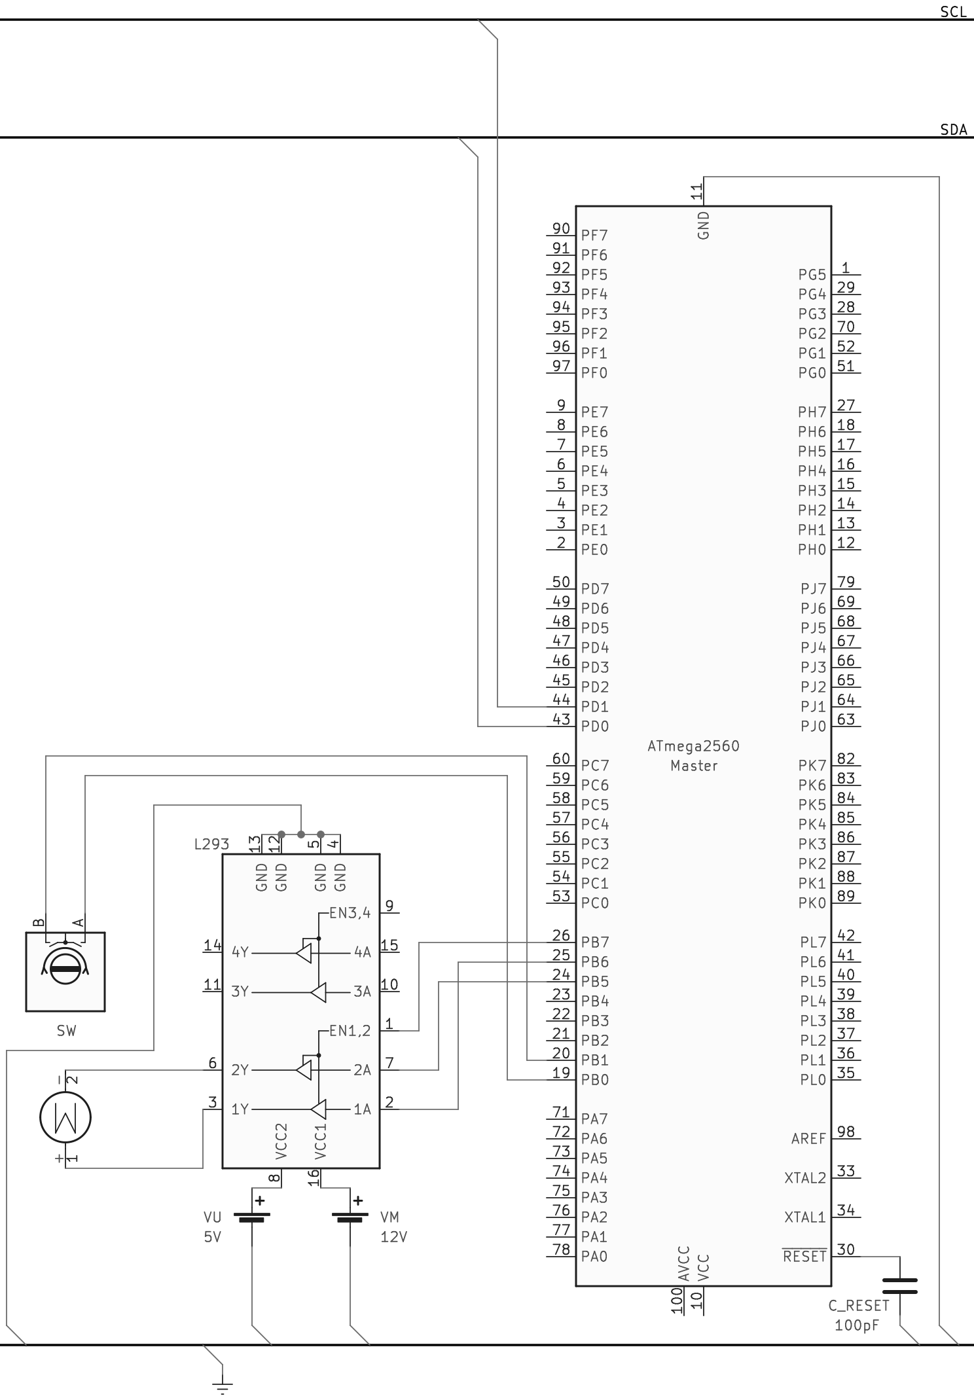
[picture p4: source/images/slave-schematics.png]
  
  \caption{Slave controller schematics}
  \label{img:slave-sch}
\end{centering}
\end{figure}

\subsection{Wiring}
The wiring correspondence for the slave controller MCU is shown in table
\ref{tab:slave-wiring}.
\begin{table}[htb]
  \begin{tabularx}{\textwidth}{c l X}
    \toprule
    Board pin & MCU pin & Description \\
    \midrule
    D20 & 44/PD1/SDA    & I2C data bus \\
    D21 & 43/PD0/SCL    & I2C clock bus \\
    D13 & 26/PB7        & PWM output to the motor driver \\
    D12 & 25/PB6        & Motor driver direction logic 1 \\
    D11 & 24/PB5        & Motor driver direction logic 2 \\
    D52 & 20/PB1/PCINT1 & Encoder phase B \\
    D53 & 19/PB0/PCINT0 & Encoder phase A, interrupt-enabled \\
    \bottomrule
  \end{tabularx}
  \caption{Slave controller wiring}
  \label{tab:slave-wiring}
\end{table}

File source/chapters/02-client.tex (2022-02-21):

\chapter{Client-side user interaction}
\label{ch:client}
A client program has been realized to manipulate the dc motors directly from
the PC. It can ping slave controllers, get and set the speed of individual
motors, and to apply all the previously set speeds for all of them at once.\\
A brief list of the client's features is given below:
\begin{itemize}
  \item Granular handling for getting and setting motors' speed
  \item Modular and extensible software architecture
  \item Terminal User Interface, implemented as a command shell
  \item Support for non-interactive use (i.e.\ scripting)
  \item Communication with master controller using the serial protocol
  \item Compatible with POSIX-compliant environments
\end{itemize}
The client is also documented with a man page, which can be found in section
\ref{sec:client-manpage}.

\section{User Interface}
The end user interacts with the whole ammc ecosystem using a text-based client.
It consists in a shell module, which I had written myself, offering some
\emph{internal commands} (hardcoded in the shell module itself) and is extended
by \emph{external commands} (found in a separated source code entity, and that
can even be compiled in a detached transaction unit).

A particular focus was made on the software architecture: indeed, every
external command can be realized standalone, and it is easy to add new
commands just by altering the \texttt{client/source/shell\_commands.c} source
file.

\section{Primitives offered}
The commands that can be used to interface with the ammc ecosystem are the
following:
\begin{description}
  \item[connect <device-path>] Connect to a master controller, given the path
    to the block device representing it
  \item[ping <slave-id>] Ping a slave controller by address
  \item[get-speed <motor-id>] Get the speed of a dc motor given its id.
    The motor id must be specified as a decimal number
  \item[set-speed <motor-id>=<speed>] Set the speed of a dc motor given its id
    The motor id must be specified as a decimal number and the speed must be
    specified in rpm
  \item[apply] Apply the previously set speed for all the dc motors
  \item[set-slave-addr] Set a new TWI address for a slave controller
\end{description}

\subsection{Non-interactive mode}
The client shell is capable of running in non-interactive (i.e.\ scripting)
mode with the \texttt{-s} option.  If so, it will parse the input from a
specified text file, or from \texttt{stdin} if not provided.  A shell launched
in non-interactive mode will not print shell prompts, and exit when end-of-file
is encountered or on command failure.

\section{Serial module}
The client's serial module has been realized using the POSIX \emph{termios}
interface. Unlike the master controller's counterpart, all its code is
reentrant, therefore multiple instances of multiple serial devices can
theoretically exist at the same time.

From the client's perspective, the master controller is seen as a file
descriptor, and the end user just have to specify the path of the block device
file representing the serial communication channel (e.g. \texttt{/dev/ttyACM0})
using the \texttt{connect} command.

\section{Specification}

\subsection{Software modules}
An exhaustive list of software modules for the client application is given
in table \ref{tab:client-spec-modules}. File paths are relative to the
\texttt{client/} directory.

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

\subsection{Modules dependency graph}
The dependency graph for the client application software modules is shown in
figure \ref{img:client-deps-graph}. The \emph{debug} module is excluded. Notice
how the dependency flow goes in one direction (from top to bottom); this is the
result of the software architecture policy used.
\begin{figure}[hbp]
\begin{centering}
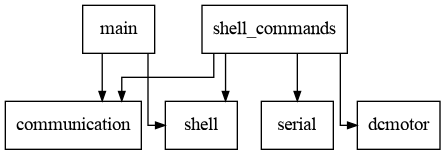
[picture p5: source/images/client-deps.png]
  
  \caption{Client application modules dependency graph}
  \label{img:client-deps-graph}
\end{centering}
\end{figure}

\section{Man page}
\label{sec:client-manpage}
{
  \ttfamily
  \import{./misc/}{manpage.tex}
}

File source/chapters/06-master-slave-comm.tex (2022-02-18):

\chapter{Master-Slave communication}
\label{ch:master-slave-comm}
The master and slave controllers communicate to each other using the I2C
bus. Naturally, the master controller is responsible for starting communication
sessions, addressing one or all the slaves.

The bitrate is set to 100kbit/s, i.e.\ the maximum speed available for the
original I2C standard\cite{i2c-ref} (excluding fast modes, which were
implemented later).

\subsection{Hardware setup}
The I2C bus itself is a pair of bus rails, named \texttt{SDA} and \texttt{SCL},
representing data and bus clock respectively.

Two $4.7 k\Omega$ resistors connects \texttt{SDA} and \texttt{SCL} to a $5V$
voltage generator and act as \emph{open-drain} resistors.

\subsection{Communication frames}
The first byte of the I2C communication frame (excluding, of course, the slave
address) is an 8-bit unsigned integer representing the command sent by the
master to the slave. The trailing data represents an argument, with its size
and shape depending on the type of command issued. Command codes, with their
specific arguments, are shown in table \ref{tab:i2c-commands}.

\begin{table}[ht]
  \begin{tabularx}{\textwidth}{c c c X}
    \toprule
    Command & Code & Arg.\ size (bytes) & Description \\
    \midrule
      \texttt{GET}       & \texttt{0x00} & - & Get the dc motor speed in rpm \\
      \texttt{SET}       & \texttt{0x01} & 2 & Set the dc motor target speed \\
      \texttt{APPLY}     & \texttt{0x02} & - & Apply the previously set target speed \\
      \texttt{PING}      & \texttt{0x03} & 1 & Ping a slave controller \\
      \texttt{SET\_ADDR} & \texttt{0x04} & 1 & Set a different I2C slave address \\
    \bottomrule
  \end{tabularx}
  \caption{Master-to-slave commands}
  \label{tab:i2c-commands}
\end{table}

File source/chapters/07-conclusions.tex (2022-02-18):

\chapter{Conclusions}
\label{ch:conclusions}
In this work I developed an electrical motor handling hardware/software
solution with modularity and extensibility in mind. In this very final chapter
I demonstrate how ammc can be used in practice and I explain how it could be
developed further in the future.

\section{Example setup}

\subsection{Hardware}
The hardware required for the example setup given here is the following:
\begin{itemize}
  \item One \emph{ATMega2560} microcontroller unit for the master controller
  \item One \emph{ATMega2560} microcontroller unit for the slave controller
  \item Two $4.7 k\Omega$ resistors for the I2C open-drain
  \item A $100 pF$ capacitor to inhibit the reset-over-serial capabilities of
    the ATMega2560 board
  \item A 150 rpm dc motor with embedded two-phase encoder
  \item An L293 h-bridge motor driver
  \item A power supply compatible with the h-bridge and motor voltage and
    power requirements (e.g.\ $12 V,\ 24 W$)
\end{itemize}

The hardware setup must be performed as shown in figures \ref{img:master-sch}
and \ref{img:slave-sch}.
The L293 driver must be powered with two independent power supplies, one at
$12V$ (for the motor output amplifier) and one at $5V$ (for the driver logic
circuit. The AVR microcontrollers can be powered using their USB sockets. The
I2C reference voltage can be set by using a $5 V$ output pin of the master
controller board.

\subsection{Software}
The software can be built and eventually flashed using GNU Make. the
\emph{avr-gcc} toolchain and the \emph{avr-libc} library are required for the
build, while \emph{avrdude} is required for flashing.

The \texttt{make} command will build all the ammc software, i.e.\ the master
and slave controllers firmwares and the client application. The \texttt{make
master-flash} and the \texttt{make slave-flash} commands will flash the master
and slave firmwares into their respective microcontrollers. The compiled client
application will be located under the \texttt{client/target} directory.

\section{Future work}

\subsection{Extended connectivity}
The extension of the master controller connectivity would make ammc suitable
for whole new range of application possibilities. For example, \emph{LoRaWAN}
and similar communication vectors would make ammc a motor management system
suitable for dc motor distributed in a wide-area. The use of multiple wired
low-level communication means such as SPI or raw serial ports would make ammc
suitable for a multi-master, multi-group setup.

\subsection{Programming API}
The client application offers a non-interactive mode for basic scriping
functionality. Thus it is good for basic automation, it is quite limited when
more complex features are required, such as an advanced use of logic or control
flow capabilities. For this purpose, the implementation of a programming API,
eventually with bindings in various languages, would make the ammc
functionality directly available to the programmer as high-level functions.

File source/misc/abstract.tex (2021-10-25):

\begin{abstract}
  Nowadays, men physical work is gradually being taken or eased by technology.
  Many solutions in this area of interest rely on the use of electrical motors
  to accomplish tasks. Furthermore, electrical motors are widely used in many
  retail products, such as toys, domotic devices and so on.

  In this work I propose, as the result of my bachelor degree apprenticeship,
  the \emph{AVR Multi Motor Control} ecosystem as a solution for the management
  of multiple dc motors. It is composed of a \emph{client} application for user
  interaction, a \emph{master} controller and multiple \emph{slave}
  controllers, each handling a single motor. The master controller manages
  slave controllers, reading and manipulating the dc motors' speed with
  granularity.

  In chapter \ref{ch:intro} I give a broad overview on the work done, focusing
  on the structure of the entire project and the approach I had relating to 
  software architecture, coding and documentation writing.

  In chapter \ref{ch:client} I discuss the client-side application, focusing on
  user interaction and software architectural characteristics.

  In chapter \ref{ch:master} I discuss the master controller, focusing on
  hardware setup and firmware internals.

  In chapter \ref{ch:slave} I discuss the slave controller, focusing on
  hardware and the software-defined Proportional-Integral-Derivative controller
  embedded in the firmware.

  In chapter \ref{ch:client-master-comm} I discuss the protocols responsible
  for the communication between the client application and the master
  controller, and how I used the underlying serial communication channel.

  In chapter \ref{ch:master-slave-comm} I explain how I used the I2C bus to
  connect the master controller to multiple slave controllers.
\end{abstract}

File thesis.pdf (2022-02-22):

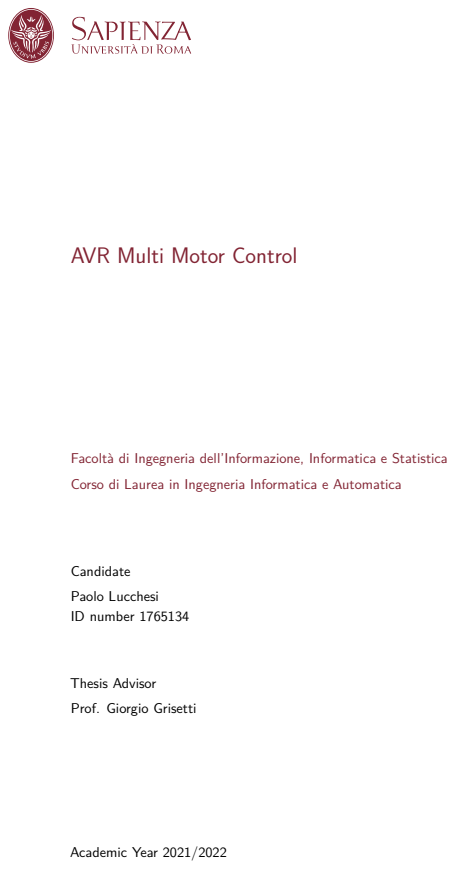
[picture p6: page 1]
Candidate; Paolo Lucchesi ID number 1765134; Academic Year 2021/2022

AVR Multi Motor Control

Facoltà di Ingegneria dell’Informazione, Informatica e Statistica
Corso di Laurea in Ingegneria Informatica e Automatica

Thesis Advisor
Prof. Giorgio Grisetti

Thesis defended on 22 February 2022
in front of a Board of Examiners composed by: Prof. Silvia Bonomi (chairman)

AVR Multi Motor Control
Bachelor’s thesis. Sapienza – University of Rome

© 2022 Paolo Lucchesi. All rights reserved

This thesis has been typeset by LATEX and the Sapthesis class.

Website: https://github.com/jcondor98/ammc

Author’s email: lucchesi.1765134@studenti.uniroma1.it

Dedicated to my family, my granddad Pietro, my mom Anna Rosa, my dad Marco, my grandmom Pierina and my sister Valentina, which I thank everyday for everything I am. To my dearest friends in Pitigliano, with whom I share some of the most beautiful memories I have.
To Nicola, with whom I have shared part of this path; he helped me in a dark period of my life and he is one of my dearest friends.

v

### Abstract

Nowadays, men physical work is gradually being taken or eased by technology. Many solutions in this area of interest rely on the use of electrical motors to accomplish tasks. Furthermore, electrical motors are widely used in many retail products, such as toys, domotic devices and so on.
In this work I propose, as the result of my bachelor degree apprenticeship, the AVR Multi Motor Control ecosystem as a solution for the management of multiple dc motors. It is composed of a client application for user interaction, a master controller and multiple slave controllers, each handling a single motor. The master controller manages slave controllers, reading and manipulating the dc motors’ speed with granularity.
In chapter 1 I give a broad overview on the work done, focusing on the structure of the entire project and the approach I had relating to software architecture, coding and documentation writing.
In chapter 2 I discuss the client-side application, focusing on user interaction and software architectural characteristics.
In chapter 3 I discuss the master controller, focusing on hardware setup and firmware internals.
In chapter 4 I discuss the slave controller, focusing on hardware and the software-defined Proportional-Integral-Derivative controller embedded in the firmware. In chapter 5 I discuss the protocols responsible for the communication between the client application and the master controller, and how I used the underlying serial communication channel.
In chapter 6 I explain how I used the I2C bus to connect the master controller to multiple slave controllers.

vii

# Contents

1 Introduction | 1
2 Client-side user interaction | 5
3 Master controller | 9

viii | Contents
4 Slave controllers | 13
5 Client-Master communication | 19
6 Master-Slave communication | 23
7 Conclusions | 25
Bibliography | 27

ix

# List of Tables

2.1 Client application software modules | 7
3.1 Master application software modules | 11
3.2 Master controller wiring | 11
4.1 Slave application software modules | 16
4.2 Slave controller wiring | 17
5.1 Packet header fields | 20
5.2 Exhaustive list of packet types | 21
5.3 Exhaustive list of packet error codes | 21
6.1 Master-to-slave commands | 23

x

# List of Figures

2.1 Client application modules dependency graph | 7
3.1 Master controller modules dependency graph | 10
3.2 Master controller schematics | 12
4.1 Slave controller modules dependency graph | 16
4.2 Slave controller schematics | 17

1

# Chapter 1

# Introduction

### 1.1 Motivation

The use of dc motors is widespread in many application fields. Often, the offered solutions are monolithic and use of very specific (and sometimes ad-hoc developed) hardware. The ammc ecosystem focuses on the use of very common, affordable and easily available hardware, such as AVR microcontrollers.
The software is designed to be modular, extensible and easily hackable by any average C programmer, so that in the future other people interested in this project can contribute or adapt ammc to fit their needings and accomplish their business logic.

### 1.2 Contributions

The ammc ecosystem offers a flexible, affordable, hackable solution for the management of multiple dc motors. It is composed of three main components:

- A client-side application
- A master controller
- One or more slave controllers

### 1.2.1 Client

The client-side application is written in C. It makes use of the POSIX standard library, and in particular the termios interface to generic serial devices. It offers a shell-fashioned terminal user interface.

2 1. Introduction

### 1.2.2 Master

The master controller is an AVR microcontroller unit. The firmware is written in C, using the avr-gcc compiler and the avr-libc standard library implementation. It dispatches user commands (taken by the client) to slave controllers.

### 1.2.3 Slave

The slave controllers are AVR microcontroller units. The firmware is written in C, using the avr-gcc compiler and the avr-libc standard library implementation. Each slave controller manages a single dc motor, taking commands by the master controller.

### 1.3 Technical approach

### 1.3.1 Software architecture

I have developed all the top-level ammc components following the principles I have learned both from my University courses[2] and my personal insights[4][6].
The client application and the microcontroller firmwares were developed following the SOLID principles, with attention on the Open-Close principle. I have put particular attention on modularity; many of the software modules found in all the ammc applications are standalone and will work out of the box if brought into other projects.
I tried to develop my software with the following policy: the core of the application should be composed of reusable, standalone modules; the business logic of the application, which obviously radically changes from project to project, should be placed in the peripheral modules and should use, when possible, interfaces for dependency inversion towards the core modules.
For example, in the master controller firmware source code I use function pointers to generalize the operations to be triggered by client commands. Naturally, such practices would have been easier and more evident with a programming language explicitly supporting the object-oriented paradigm (e.g. C++).

### 1.3.2 Documentation

Documentation is paramount in any software project; Damian Conway once said: ”Documentation is a love letter that you write to your future self”. I did my best to write precise and exhaustive documentation for every software piece I realized.

1.3 Technical approach | 3

This thesis is by itself a document dealing with every aspect of the ammc project. The README.md file in the root directory of the repository offers a more concise resume.
All the source code (the head files in particular) are exhaustively documented with doxygen, a tool which automatically converts properly formatted comments found in the code into technical documentation; such resource is available in the gh-pages git development branch and is hosted using GitHub Pages.
The client-side application is documented with a Unix man page, which can also be found in this thesis in section 2.5.

5

# Chapter 2

# Client-side user interaction

A client program has been realized to manipulate the dc motors directly from the PC. It can ping slave controllers, get and set the speed of individual motors, and to apply all the previously set speeds for all of them at once.
A brief list of the client’s features is given below:
- Granular handling for getting and setting motors’ speed
- Modular and extensible software architecture
- Terminal User Interface, implemented as a command shell
- Support for non-interactive use (i.e. scripting)
- Communication with master controller using the serial protocol
- Compatible with POSIX-compliant environments

The client is also documented with a man page, which can be found in section 2.5.

### 2.1 User Interface

The end user interacts with the whole ammc ecosystem using a text-based client. It consists in a shell module, which I had written myself, offering some internal commands (hardcoded in the shell module itself) and is extended by external commands (found in a separated source code entity, and that can even be compiled in a detached transaction unit).
A particular focus was made on the software architecture: indeed, every external command can be realized standalone, and it is easy to add new commands just by altering the client/source/shell_commands.c source file.

6 2. Client-side user interaction

### 2.2 Primitives offered

The commands that can be used to interface with the ammc ecosystem are the following:

connect <device-path> Connect to a master controller, given the path to the block device representing it

ping <slave-id> Ping a slave controller by address

get-speed <motor-id> Get the speed of a dc motor given its id. The motor id must be specified as a decimal number

set-speed <motor-id>=<speed> Set the speed of a dc motor given its id The motor id must be specified as a decimal number and the speed must be specified in rpm

apply Apply the previously set speed for all the dc motors

set-slave-addr Set a new TWI address for a slave controller

### 2.2.1 Non-interactive mode

The client shell is capable of running in non-interactive (i.e. scripting) mode with the -s option. If so, it will parse the input from a specified text file, or from stdin if not provided. A shell launched in non-interactive mode will not print shell prompts, and exit when end-of-file is encountered or on command failure.

### 2.3 Serial module

The client’s serial module has been realized using the POSIX termios interface. Unlike the master controller’s counterpart, all its code is reentrant, therefore multiple instances of multiple serial devices can theoretically exist at the same time.
From the client’s perspective, the master controller is seen as a file descriptor, and the end user just have to specify the path of the block device file representing the serial communication channel (e.g. /dev/ttyACM0) using the connect command.

2.4 Specification | 7

### 2.4 Specification

### 2.4.1 Software modules

An exhaustive list of software modules for the client application is given in table
2.1. File paths are relative to the client/ directory.
Module | Description | Files
communication | Top-level | communication
routines

include/communication.h,
source/communication.c
crc | CRC generation and check-
ing routines

include/crc.h,
source/crc.c
debug | Debug facilities | include/debug.h
main | Main client application rou-
tine

source/main.c

packet | Packet generation and ma-
nipulation routines

include/packet.h,
source/packet.c
ringbuffer Circular buffer data structure include/ringbuffer.h, source/ringbuffer.c
serial | Serial communication layer | include/serial.h,
source/serial.c
shell | Main program shell with
built-in commands

include/shell.h,
source/shell.c
shell_commands External commands to interact with the master controller

source/shell_commands.c

Table 2.1. Client application software modules

### 2.4.2 Modules dependency graph

The dependency graph for the client application software modules is shown in figure 2.1. The debug module is excluded. Notice how the dependency flow goes in one direction (from top to bottom); this is the result of the software architecture policy used.

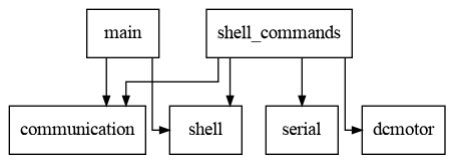
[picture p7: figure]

Figure 2.1. Client application modules dependency graph

8 2. Client-side user interaction

### 2.5 Man page

NAME

ammc — AVR Temperature Monitor client

SYNOPSIS

ammc [-s [script]] [-c device-file] ammc -h

DESCRIPTION

ammc is a multi-motor control device realized with an AVR microcontroller; this program is an ad-hoc, tui client to interface it. The ammc device is designed to work with DC motors with an embedded or external encoder.

Options

-c device-file | Connect to the device identified by device-file (e.g. /dev/ttyACM0)
-s [script] | Execute in script mode (do not print prompt, exit on error
etc...), being | script a file containing a command each line. If
script is not given, | standard input is used
-h | Display a help message and exit

Commands

help [command] Show help, also for a specific command if an argument is given

connect <device_path> Connect to an ammc Master MCU given its device file (usually under /dev)

disconnect | Close an existing connection - Has no effect on the device
ping <motor-id> | Ping a slave controller by id
get-speed <motor-id> | Get the speed of a DC motor in RPM
set-speed <motor-id>=<value> | Set the speed of a DC motor in RPM

AUTHOR

Paolo Lucchesi <paololucchesi@protonmail.com> https://www.github.com/jcondor98/ammc

9

# Chapter 3

# Master controller

The master controller handles all the slave controllers, dispaching arbitrary commands to them using the I2C protocol. It also communicates directly with the client application via serial port.

### 3.1 Hardware setup

The master controller itself is an AVR ATMega2560 microcontroller unit[1]. This particular MCU has features convenient for this project, such as:

- I2C dedicated hardware subsystem
- Serial-over-USB bridge
- Relatively powerful specifications for future feature adding
- Plenty of timers and outgoing power pins

A 100pF capacitor is used to block the reset capabilities of the serial-over-usb controller and enhance the serial channel reliability. Two 4.7kΩ resistors are used as open-drain resistors for the I2C bus.

### 3.2 I2C setup

The I2C protocol is used to communicate with slave controllers. Transmission and reception are interrupt-based, and no busy-wait is used.
The I2C module has broadcasting capabilities, according to the informations found in the I2C standard[5]; the broadcasting (i.e. general call) address used is 0x00. As stated by the standard, the master controller has no knowledge on the number or identity of the slaves receiving a broadcast frame.

10 3. Master controller

### 3.3 Power management

An own-written wrapper for the avr-gcc standard library’s sleep functionalities is used for power management. By default, the master controller is in idle mode, and it is awakened by any raised interrupt, e.g. by incoming serial or I2C data; then, its main loop routine is executed and, if no other operations must be performed, it returns in idle mode.
The master controller is also put in idle when waiting for data inside serial or I2C routines; this is possible thanks to the interrupt-driven nature of the aforementioned modules.

### 3.4 Specification

### 3.4.1 Software modules

An exhaustive list of software modules for the master controller firmware is given in table 3.1. File paths are relative to the master/ directory.

### 3.4.2 Modules dependency graph

The dependency graph for the master controller’s software modules is shown in figure 3.1. The debug module is excluded. Notice how the dependency flow goes in one direction (from top to bottom); this is the result of the software architecture policy used.

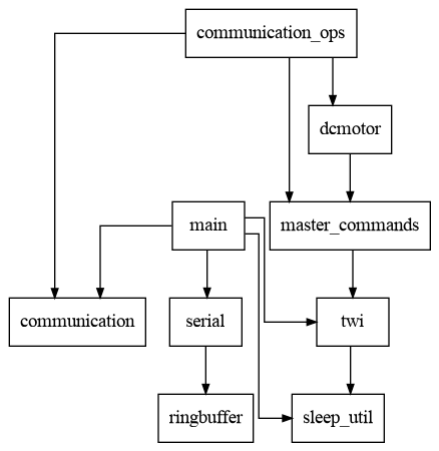
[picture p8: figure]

Figure 3.1. Master controller modules dependency graph

3.4 Specification | 11
Module | Description | Files
communication | Top-level communication routines | include/communication.h, source/communication.c
communication_ops Application-specific | use
| cases | source/communication_ops.c
crc | CRC generation and check- ing routines | include/crc.h, source/crc.c
dcmotor | Top-level routines for inter- facing slave controllers | include/dcmotor.h, source/dcmotor.c
main | Main and power manage- ment routines | source/main.c
master_commands | Interface to issue com- mands to slave controllers | source/master_commands.c, include/master_commands.h
packet | Packet generation and ma- nipulation routines | include/packet.h, source/packet.c
ringbuffer | Circular buffer data struc-
| ture | include/ringbuffer.h, source/ringbuffer.c
serial | Serial communication layer include/serial.h,
| | source/serial.c
sleep_util | Wrapper for the avr-libc power management facili-
| ties | include/sleep_util.h
twi | I2C/TWI communication layer

include/twi.h,
source/twi.c
Table 3.1. Master application software modules

### 3.4.3 Circuit schematics

The complete circuit schematics for the master controller and all its components is shown in figure 3.2.

### 3.4.4 Wiring

The wiring correspondence for the master controller MCU is shown in table 3.2.

Board pin MCU pin | Description
D20 | 44/PD1/SDA I2C data bus
D21 | 43/PD0/SCL | I2C clock bus
RESET | RESET | On-board MCU reset pin
Table 3.2. Master controller wiring

12 3. Master controller

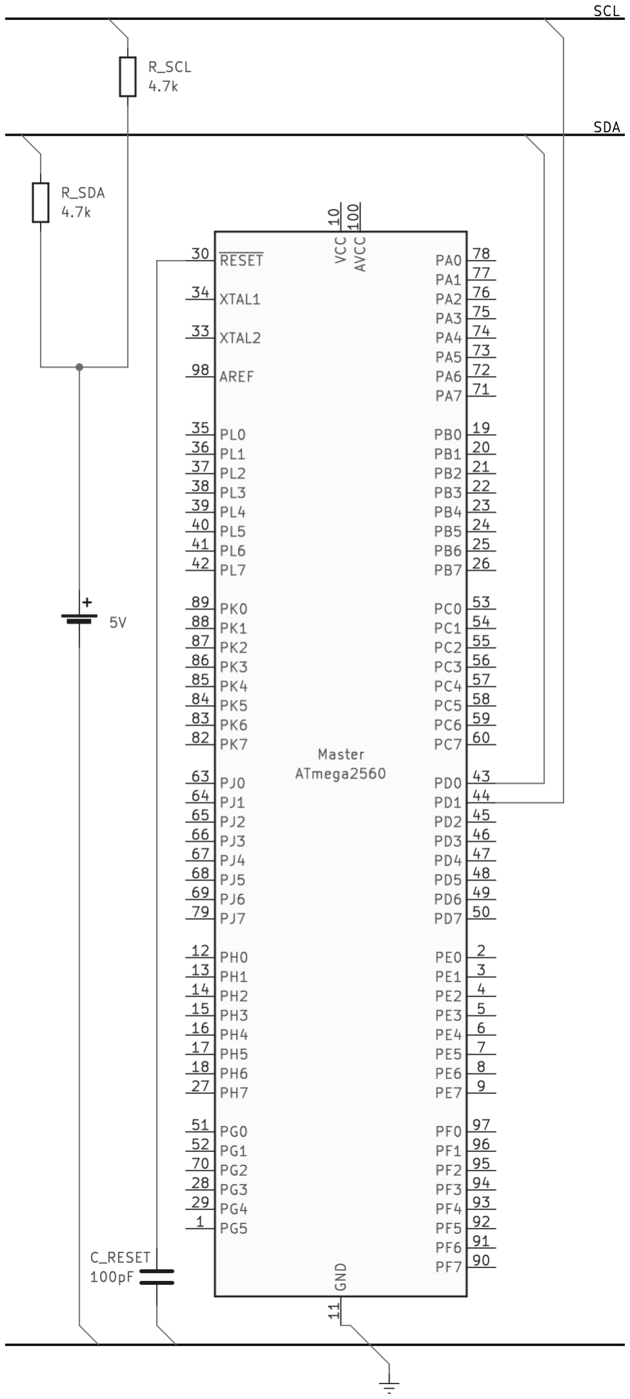
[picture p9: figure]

Figure 3.2. Master controller schematics

13

# Chapter 4

# Slave controllers

Each slave controller directly handles a single dc motor, receiving commands from the master controller via I2C. It must offer an interface to get and manipulate its motor’s speed.
The slave controller produces a PWM wave having a duty cycle consistent with the speed (given in RPM) specified by the end user in order to control its motor. Furthermore, it comes with a software Proportional-Integral-Derivative controller to correct the bias between target and actual motor speeds.

### 4.1 Hardware setup

The slave controller itself is an AVR ATMega2560 microcontroller unit[1], which offers the following features of interest:

- Dedicated I2C hardware subsystem
- PWM-capable 8-bit and 16-bit timers

Apart from the motor itself (along with its power supply and its dedicated H-bridge control board) no additional hardware is used.

### 4.2 I2C setup

A slave controller communicates with the master controller using the I2C protocol. As for the master controller, both transmission and reception are interrupt-based. The slave controller is always passive on the bus, waiting to be addressed by the master.

14 4. Slave controllers

### 4.2.1 Dynamic I2C addressing

Each slave controller needs a unique I2C address. Basically, there are two ways to assign an arbitrary address to a slave.
The first and most trivial one is to define the TW_DEFAULT_ADDR macro to the desired address when building the slave controller firmware. This solution is impractical for obvious reasons and should be avoided.
The second method is to connect the master and slave controllers via I2C and the master controller with the client via serial. Then the set-slave-addr command can be used to change the I2C address to the desired one. The changes take place immediately, as the slave controller’s I2C software module is reinitialized, and they will be saved in the EEPROM embedded into the AVR microcontroller for durability.

### 4.3 Proportional-Integral-Derivative controller

An own-written, software-defined Proportional-Integral-Derivative controller is used to correct the actual motor speed. As for any PID device, the equation controlling the error is:

u(t) = Kpe(t) + Ki

∫ t

t0

e(τ ) dτ + Kd

d
dt e(t) | (4.1)

being:

- e(t) the measured speed error
- u(t) the PID control variable
- Kp the proportional gain
- Ki the integral gain
- Kd the derivative gain

### 4.3.1 Measuring speed

For actual PID capabilities, the slave controller must sample the actual speed of the dc motor at fixed intervals. Therefore, the motor must have an embedded, two-phase digital encoder.
In fact, one phase is wired to an interrupt-enabled input pin, so the slave controller is notified immediately when an encoder signal (raising edge) is generated. Every sampling interval, the PID routine takes the motor’s actual position (measured by the cumulative number of encoder triggers) and computes its real speed.

4.4 Power management | 15

### 4.3.2 Approximations

Of course, a software digital PID controller can not compute exact integrals and derivatives, so it is necessary to use approximation.
The integral operation is approximated using Riemann sums. Given a time delta ∆t (the actual speed sampling interval in this particular case), the approximating law is defined as:
∫ t

t0

e(τ ) dτ ≈

∑n

k=1

e(t

∗
k
) · ∆t | (4.2)

The derivative operation is approximated using its definition[3]:

d
dt e(t) = lim
∆t→0

e(t + ∆t) − e(t)
∆t

=⇒

d
dt e(t) ≈

e(t + ∆t) − e(t)
∆t
| (4.3)

being ∆t a time delta (again, the actual speed sampling interval).

### 4.4 Power management

The same avr-libc wrapper written for the master controller power management is used. By default, the slave controller is in idle mode, and it is awakened by any raised interrupt. The main loop routine is executed and the idle mode is entered again. Like for the master controller, the slave is put in idle when waiting for the I2C routines to return.
The AVR idle mode allows the timers to work, so the slave controller can generate PWM waves to control the motors, even while sleeping.

### 4.5 Specification

### 4.5.1 Software modules

An exhaustive list of software modules for the slave controllers firmware is given in table 4.1. File paths are relative to the slave/ directory.

### 4.5.2 Modules dependency graph

The dependency graph for the slave controllers’ software modules is shown in figure 4.1. The debug module is excluded.

16 4. Slave controllers

Module | Description | Files
command | Interface to handle commands issued by the master controller | source/command.c, include/command.h
dcmotor | High-level interface to the dc
| motor | source/dcmotor.c, include/dcmotor.h

dcmotor_phy HAL interface for direct (i.e.

| physical) dc motor handling | source/dcmotor_phy.c, include/dcmotor_phy.h, include/dcmotor_phy_params.h
dcmotor_pid PID controller routines | source/dcmotor_pid.c,
| | include/dcmotor_pid.h
main | Main and power management routines | source/main.c
sleep_util | Wrapper for the avr-libc power management facilities | include/sleep_util.h
twi | I2C/TWI communication layer include/twi.h,
| | source/twi.c
Table 4.1. Slave application software modules

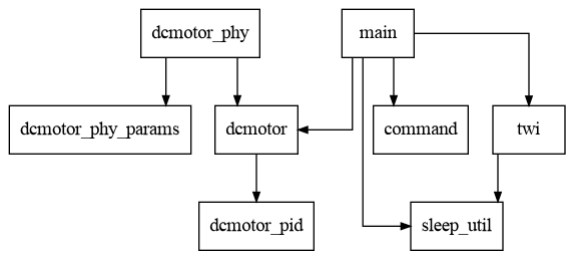
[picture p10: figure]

Figure 4.1. Slave controller modules dependency graph

### 4.5.3 Circuit schematics

The complete circuit schematics for the slave controller and all its components is shown in figure 4.2. This circuit can be repeated multiple times (up to 126) in a single ammc ecosystem.

### 4.5.4 Wiring

The wiring correspondence for the slave controller MCU is shown in table 4.2.

4.5 Specification | 17
Board pin MCU pin | Description
D20 | 44/PD1/SDA | I2C data bus
D21 | 43/PD0/SCL | I2C clock bus
D13 | 26/PB7 | PWM output to the motor driver
D12 | 25/PB6 | Motor driver direction logic 1
D11 | 24/PB5 | Motor driver direction logic 2
D52 | 20/PB1/PCINT1 Encoder phase B
D53 | 19/PB0/PCINT0 Encoder phase A, interrupt-enabled
Table 4.2. Slave controller wiring

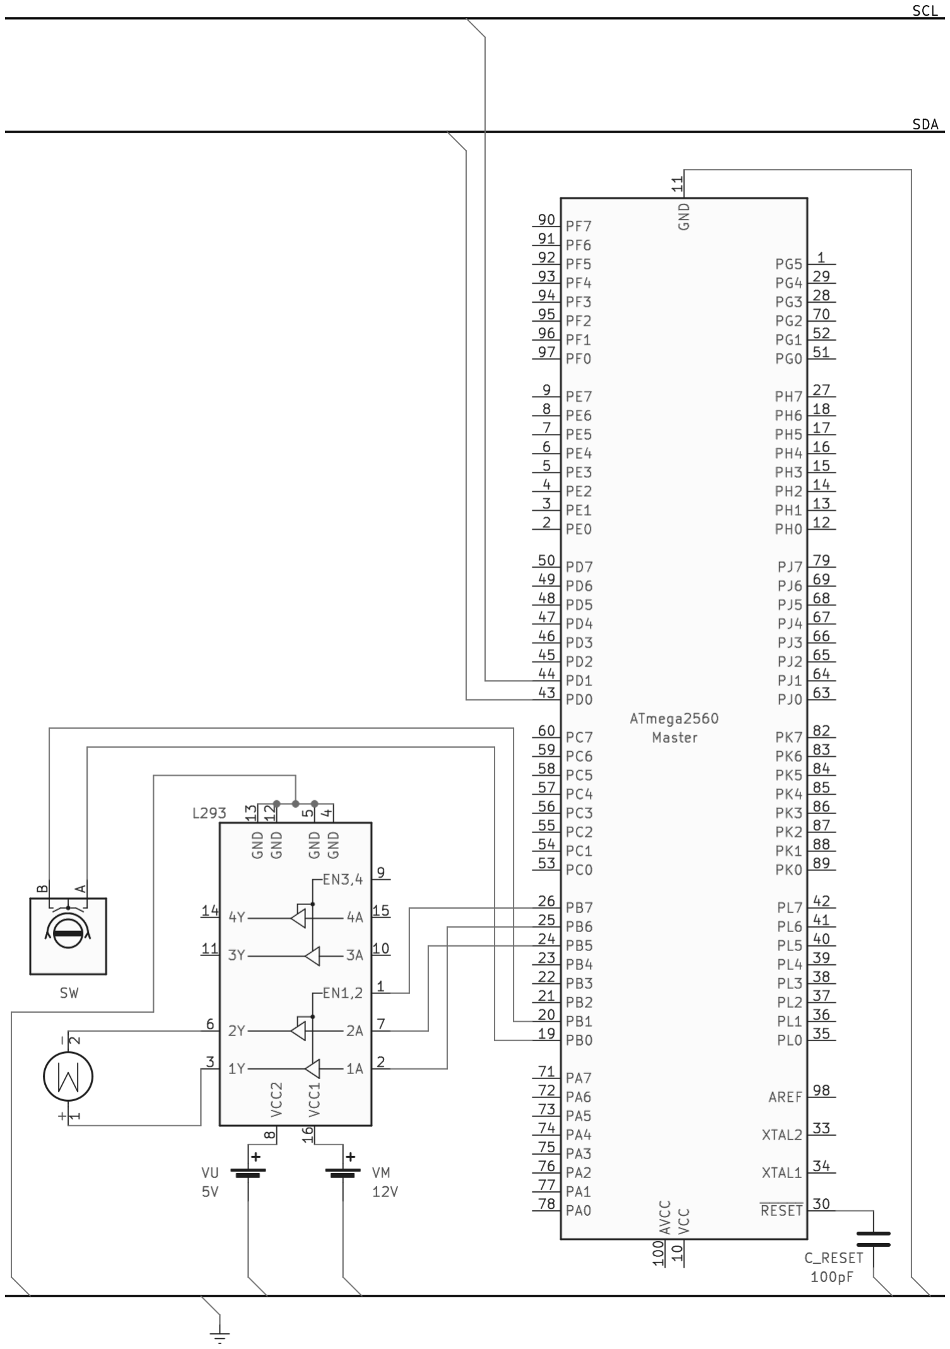
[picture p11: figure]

Figure 4.2. Slave controller schematics

19

# Chapter 5

# Client-Master communication

The client application and the master controller communicate over a protocol built on top of the serial-over-usb layer. Such protocol is completely binary and packetbased. Each packet has a variable length (with a total maximum size of 36 bytes) and its integrity is checked with a trailing CRC-8 checksum.
The protocol comes with a simple handshaking mechanism, in order to synchronize the packet IDs between endpoints and as a shallow proof of correct functionality of the communication layers.

### 5.1 Serial layer

Data exchange between client and master relies on the serial protocol. For the client application, the termios library is used, while for the master controller the (hardware) serial subsystem offered by the AVR microcontroller[1] is used.
The serial communication is set up as follows:
- Baud rate of 115200 baud, double speed transmission
- 8 bit frame width
- No start bits, 1 stop bit (i.e. 8N1)
- No embedded parity bit

For the master controller, both transmission and reception are interrupt-driven, so the communication main routine is only called when data is actually available.

### 5.2 Packet headers

Each packet’s metadata is contained in a fixed size header, composed as describe in table 5.1.

20 5. Client-Master communication

### 5.2.1 Identifiers

The id field stores the packet identifier, which is incremental and can be repeated in a single communication session. When the handshake is performed, or when any endpoint raises an error (issuing a NAK packet), the id is reset to zero for both sides. Each ACK and NAK packet is generated with the same id of the referred packet (see 5.3 for further informations).

### 5.2.2 Packet types

The type field stores the packet type. An exhaustive list of packet types is given in table 5.2

### 5.2.3 Motor selector

The selector field is used to store the identifier for the dc motor to manipulate. This field is used in GET_SPEED and SET_SPEED packets.
For NAK packets, instead, the selector field is used to store error codes (found in table 5.3).
For all the other packet types, the selector field is ignored.

### 5.3 Acknowledgements and errors

A communication endpoint must wait for an acknowledgement message from the counterpart once it sent a packet in order to send a new one. ACK and NAK packets do not bring any data.
When a packet arrives, it is checked for integrity and sanity. If it is sane, then an ACK packet is sent; if not, then a NAK packet is sent. ACK and NAK packets are simply discarded if corrupted in some way.
A NAK packet uses the selector field to send to the other endpoint the error code describing what happened on its side. Error codes are listed in table 5.3.
Field | Size (bits) Description
id | 8 | Packet ID
type | 8 | Packet type
selector | 8 | Selector for DC motors. Also used to store error codes in
| | NAK packets
size | 8 | Total packet size, including header and checksum
Table 5.1. Packet header fields

5.3 Acknowledgements and errors | 21
Type | Code Description
NULL | 0x00 | Reserved, never use
HND | 0x01 | Handshake
ACK | 0x02 | Acknowledgement
NAK | 0x03 | Communication error
ECHO | 0x04 | Echo between client and master (debug only)
PING | 0x05 | Ping a slave controller by address
GET_SPEED | 0x06 | Get the current speed for a dc motor
SET_SPEED | 0x07 | Set (and apply) the speed for a dc motor
APPLY | 0x08 | Tell all the slaves to apply the previously set speeds
DAT | 0x09 | Primarily used for responses from the AVR device
SET_ADDR | 0x0A | Change the I2C address of a slave
LIMIT | 0x0B | Used for sanity checks - Must have highest value
Table 5.2. Exhaustive list of packet types
Error | Code Description
SUCCESS | 0x00 | No errors encountered
ID_MISMATCH | 0x01 | Id of received packet is not consistent
CORRUPTED_CHECKSUM | 0x02 | Checksum mismatch, received packet is cor-
| | rupted
WRONG_TYPE | 0x03 | Received packet has invalid type
TOO_BIG | 0x04 | Received packet has invalid size (too big)
Table 5.3. Exhaustive list of packet error codes

23

# Chapter 6

# Master-Slave communication

The master and slave controllers communicate to each other using the I2C bus. Naturally, the master controller is responsible for starting communication sessions, addressing one or all the slaves.
The bitrate is set to 100kbit/s, i.e. the maximum speed available for the original I2C standard[5] (excluding fast modes, which were implemented later).

### 6.0.1 Hardware setup

The I2C bus itself is a pair of bus rails, named SDA and SCL, representing data and bus clock respectively.
Two 4.7kΩ resistors connects SDA and SCL to a 5V voltage generator and act as open-drain resistors.

### 6.0.2 Communication frames

The first byte of the I2C communication frame (excluding, of course, the slave address) is an 8-bit unsigned integer representing the command sent by the master to the slave. The trailing data represents an argument, with its size and shape depending on the type of command issued. Command codes, with their specific arguments, are shown in table 6.1.

Command Code Arg. size (bytes) Description
GET | 0x00 | - | Get the dc motor speed in rpm
SET | 0x01 | 2 | Set the dc motor target speed
APPLY | 0x02 | - | Apply the previously set target speed
PING | 0x03 | 1 | Ping a slave controller
SET_ADDR | 0x04 | 1 | Set a different I2C slave address
Table 6.1. Master-to-slave commands

25

# Chapter 7

# Conclusions

In this work I developed an electrical motor handling hardware/software solution with modularity and extensibility in mind. In this very final chapter I demonstrate how ammc can be used in practice and I explain how it could be developed further in the future.

### 7.1 Example setup

### 7.1.1 Hardware

The hardware required for the example setup given here is the following:

- One ATMega2560 microcontroller unit for the master controller
- One ATMega2560 microcontroller unit for the slave controller
- Two 4.7kΩ resistors for the I2C open-drain
- A 100pF capacitor to inhibit the reset-over-serial capabilities of the ATMega2560 board
- A 150 rpm dc motor with embedded two-phase encoder
- An L293 h-bridge motor driver
- A power supply compatible with the h-bridge and motor voltage and power requirements (e.g. 12V, 24W)

The hardware setup must be performed as shown in figures 3.2 and 4.2. The L293 driver must be powered with two independent power supplies, one at 12V (for the motor output amplifier) and one at 5V (for the driver logic circuit. The AVR microcontrollers can be powered using their USB sockets. The I2C reference voltage can be set by using a 5V output pin of the master controller board.

26 7. Conclusions

### 7.1.2 Software

The software can be built and eventually flashed using GNU Make. the avr-gcc toolchain and the avr-libc library are required for the build, while avrdudeis required for flashing.
The make command will build all the ammc software, i.e. the master and slave controllers firmwares and the client application. The make master-flash and the make slave-flash commands will flash the master and slave firmwares into their respective microcontrollers. The compiled client application will be located under the client/target directory.

### 7.2 Future work

### 7.2.1 Extended connectivity

The extension of the master controller connectivity would make ammc suitable for whole new range of application possibilities. For example, LoRaWAN and similar communication vectors would make ammc a motor management system suitable for dc motor distributed in a wide-area. The use of multiple wired low-level communication means such as SPI or raw serial ports would make ammc suitable for a multi-master, multi-group setup.

### 7.2.2 Programming API

The client application offers a non-interactive mode for basic scriping functionality. Thus it is good for basic automation, it is quite limited when more complex features are required, such as an advanced use of logic or control flow capabilities. For this purpose, the implementation of a programming API, eventually with bindings in various languages, would make the ammc functionality directly available to the programmer as high-level functions.

27

# Bibliography

[1] Atmel. Atmel ATmega640/V-1280/V-1281/V-2560/V-2561/V datasheet, 2014.
[2] Giuseppe De Giacomo. | Corso di Fondamenti di Informatica 2 - Proget-
tazione del Software. | https://sites.google.com/a/diag.uniroma1.it/
fondamenti-di-informatica-ii-progettazione-del-software-2017-18/, (https://sites.google.com/a/diag.uniroma1.it/fondamenti-di-informatica-ii-progettazione-del-software-2017-18/) 2018.
[3] Doron Levy. Introduction to Numerical Analysis. http://math.umd.edu/~dlevy/classes/amsc460/na-notes.pdf, (http://math.umd.edu/~dlevy/classes/amsc460/na-notes.pdf) 2017.
[4] Robert C. Martin. Clean Architecture: A Craftsman’s Guide to Software Structure and Design. Addison-Wesley, 2017.
[5] Philips Semiconductors. The I2C-bus Specification, 2000.
[6] Bjarne Stroustrup. The C++ Programming Language. Addison-Wesley, 4th edition, 2013.

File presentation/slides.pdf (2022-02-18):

# AVR Multi Motor Control

# Paolo Lucchesi

Paolo Lucchesi

AVR Multi Motor Control

# AVR Multi Motor Control is an electrical motor management hardware/software ecosystem composed of: A text-based client application One master controller One or more slave controllers

Text-based client application for POSIX environments Master and Slave(s) controller firmware Fully binary Client-Master communication protocol on top of the serial interface Fully binary Master-Slave communication protocol on top of the I2C interface Up to 126 DC motors (limited by 7-bit I2C Slave addressing, 0x00 is reserved) Ability to get and set the DC motors speed, individually Software defined PID controller embedded in each Slave controller

# Focus on modularity Keeping SOLID principles in mind

# Extensibility through the Open-Close Principle Attention on module call directions following the Single Responsability Principle

# Exhaustive documentation on multiple depths

# README.md file in the git repository Source code documentation generated with doxygen Client application’s man page Bachelor degree thesis

# GNU Make build system Absence of third-party non-standard libraries

# Granular handling for getting and setting motors’ speed Terminal User Interface implemented as a command shell Support for non-interactive use (i.e. scripting) Communication with master controller using the serial protocol Compatible with POSIX-compliant environments Comes with a man page

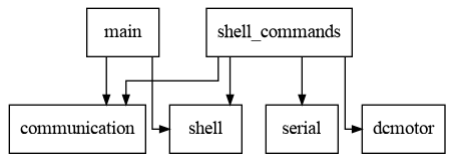
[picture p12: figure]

# Figure: Client application modules dependency graph

# External commands allow to interface the master controller:

## connect <device-path>

## ping <motor-id>

## get-speed <motor-id>

## set-speed <motor-id>=<speed>

## apply

## set-slave-addr

# Is itself an ATMega2560 microcontroller unit Interfaces the client applications with the slave controllers Communicates with the client via serial Communicates with slaves via I2C Interrupt-driven communication Comes with a power saving policy

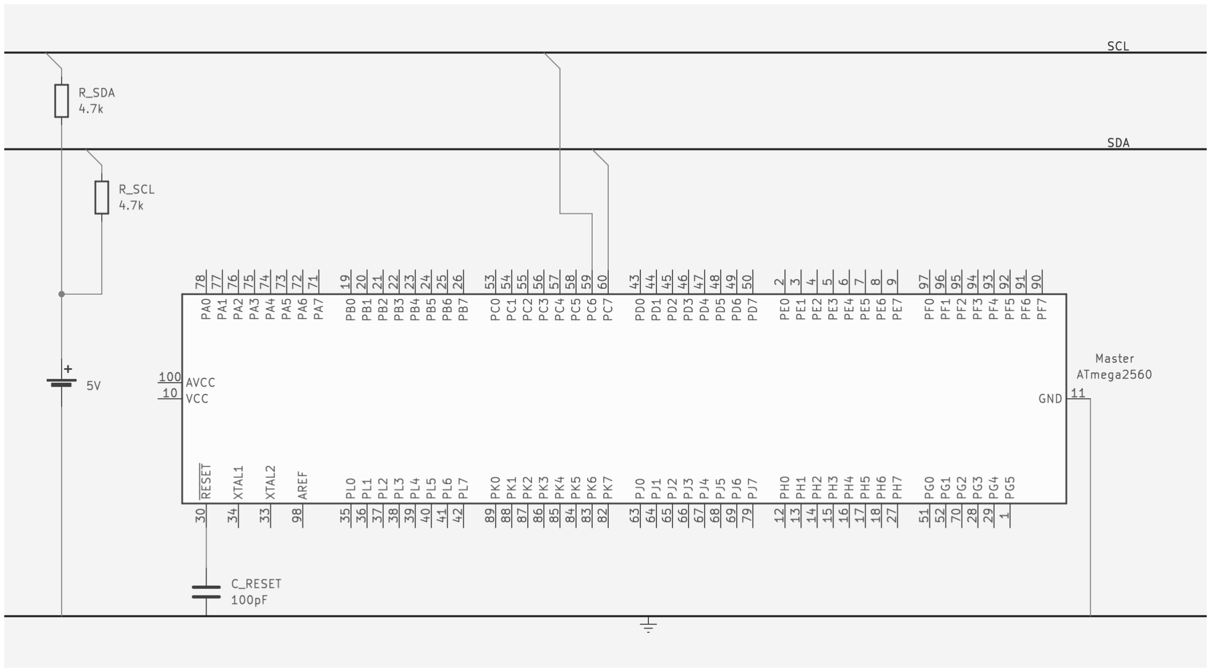
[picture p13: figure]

# Figure: Master controller schematics


# Figure: Master controller firmware modules dependency graph

# Is itself an ATMega2560 microcontroller unit Manages a single dc motor Communicates with the master controller using the I2C interface Execute commands issued by the master controller Embedded software-defined Proportional-Integral-Derivative controller

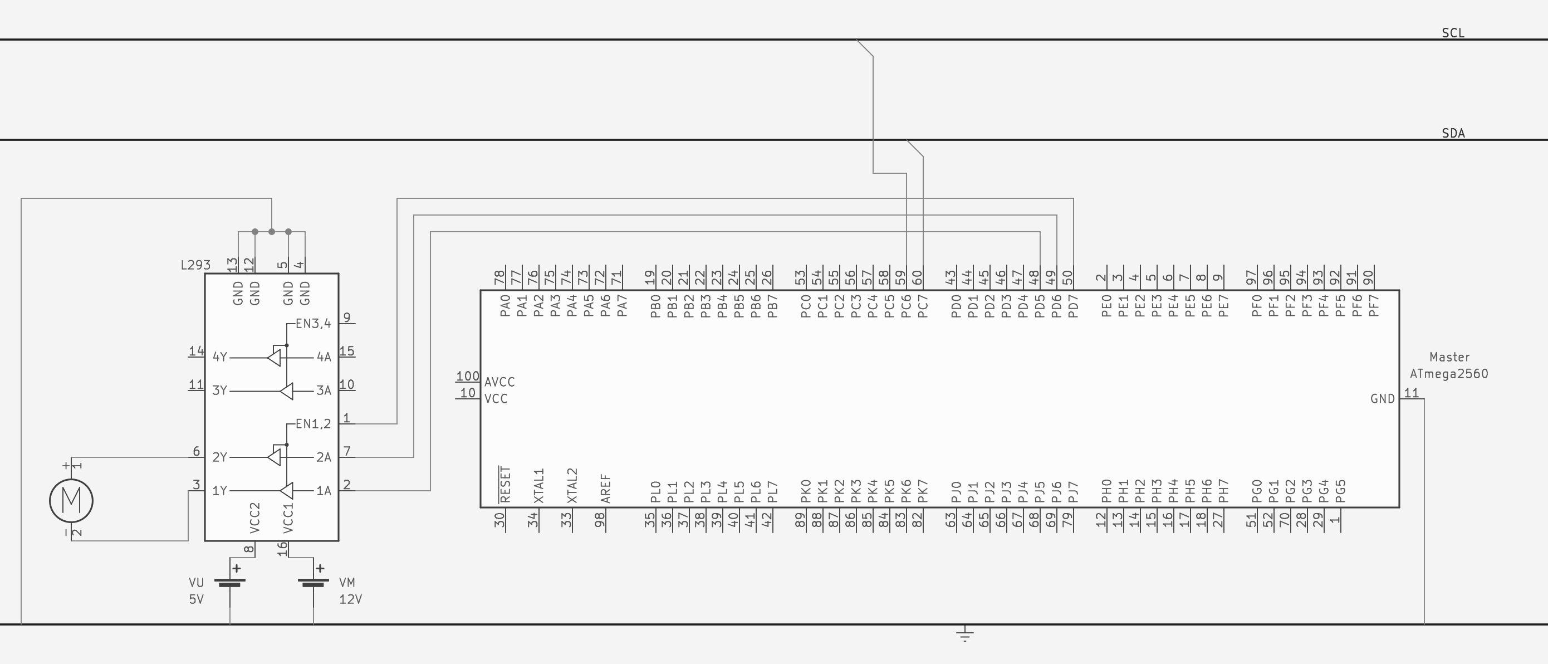
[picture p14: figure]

# Figure: Slave controller schematics

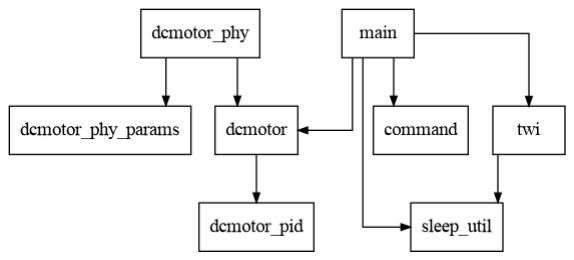
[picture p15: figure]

# Figure: Slave controller firmware modules dependency graph

# Built on top of the serial interface Completely binary Packet-based Packet integrity is checked via CRC-8 checksum Interrupt-driven for the master controller

# Each packet is composed of: A header containing:

# Packet id Packet type Whole packet size DC motor selector

# An eventual body A trailing CRC-8 checksum

Type | Actual value
COM_TYPE_NULL | 0x00
COM_TYPE_HND | 0x01
COM_TYPE_ACK | 0x02
COM_TYPE_NAK | 0x03
COM_TYPE_ECHO | 0x04
COM_TYPE_PING | 0x05
COM_TYPE_GET_SPEED | 0x06
COM_TYPE_SET_SPEED | 0x07
COM_TYPE_APPLY | 0x08
COM_TYPE_DAT | 0x09
COM_TYPE_SET_ADDR | 0x0A
COM_TYPE_LIMIT | 0x0B

# Master-Slave architecture Completely binary Interrupt-driven for both master and slaves Broadcasting capabilities through the general-call address 0x00 Follows the original Philips I2C specification (year 2000)

# The communication frames is composed of two parts: A heading byte representing the master command An optional command argument

Command | Code
CMD_GET | 0x00
CMD_SET | 0x01
CMD_APPLY | 0x02
CMD_PING | 0x03
CMD_SET_ADDR | 0x04

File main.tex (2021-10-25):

% Bachelor Degree Thesis - Paolo Lucchesi
% !TeX encoding = UTF-8
% !TeX program = pdflatex
% !TeX spellcheck = en_US

\documentclass[binding=0.6cm,Lau]{sapthesis}
\usepackage{microtype}
\usepackage[english]{babel}
\usepackage[utf8]{inputenc}
\usepackage{hyperref}
\usepackage{tabularx}
\usepackage{fontspec}
\usepackage{setspace}
\usepackage{import}

\setmainfont{TeX Gyre Pagella}
\onehalfspacing

\graphicspath{{./images/}}

\makeatletter
\def\maxwidth#1{\ifdim\Gin@nat@width>#1 #1\else\Gin@nat@width\fi}
\makeatother

\hypersetup{pdftitle={AVR Multi Motor Control},pdfauthor={Paolo Lucchesi}}

\title{AVR Multi Motor Control}
\author{Paolo Lucchesi}
\IDnumber{1765134}
\course{Ingegneria Informatica e Automatica}
\courseorganizer{Facoltà di Ingegneria dell'Informazione, Informatica e Statistica}
\AcademicYear{2021/2022}
\copyyear{2021}
\advisor{Prof. Giorgio Grisetti}
\advisor{Drs. Barbara Bazzana}
\reviewerlabel{Reviewer}
\reviewer{Prof. Silvia Bonomi}
\authoremail{lucchesi.1765134@studenti.uniroma1.it}
\website{https://github.com/jcondor98/ammc}

\begin{document}

\frontmatter
\maketitle

\dedication{
Dedicated to my family, my granddad Pietro, my mom Anna Rosa, my dad Marco,
my grandmom Pierina and my sister Valentina, which I thank everyday for
everything I am.\\
To my dearest friends in Pitigliano, with whom I share some of the most
beautiful memories I have.\\
To Nicola, with whom I have shared part of this path; he helped me in a
dark period of my life and he is one of my dearest friends.
}

\import{./misc}{abstract.tex}

\tableofcontents
\listoffigures
\listoftables

\mainmatter

\import{./chapters/}{introduction.tex}
\import{./chapters/}{client.tex}
\import{./chapters/}{master.tex}
\import{./chapters/}{slave.tex}
\import{./chapters/}{client-master-comm.tex}
\import{./chapters/}{master-slave-comm.tex}
\import{./chapters/}{conclusions.tex}

\backmatter
\cleardoublepage
\phantomsection % Give this command only if hyperref is loaded

\addcontentsline{toc}{chapter}{\bibname}
\bibliographystyle{plain}
\bibliography{main}

\end{document}

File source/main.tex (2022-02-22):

% Bachelor Degree Thesis - Paolo Lucchesi
% !TeX encoding = UTF-8
% !TeX program = pdflatex
% !TeX spellcheck = en_US

\documentclass[binding=0.6cm,Lau]{sapthesis}
\usepackage{microtype}
\usepackage[english]{babel}
\usepackage[utf8]{inputenc}
\usepackage{hyperref}
\usepackage{tabularx}
\usepackage{fontspec}
\usepackage{setspace}
\usepackage{import}

\setmainfont{TeX Gyre Pagella}
\onehalfspacing

\graphicspath{{./images/}}

\makeatletter
\def\maxwidth#1{\ifdim\Gin@nat@width>#1 #1\else\Gin@nat@width\fi}
\makeatother

\hypersetup{pdftitle={AVR Multi Motor Control},pdfauthor={Paolo Lucchesi}}

\title{AVR Multi Motor Control}
\author{Paolo Lucchesi}
\IDnumber{1765134}
\course{Ingegneria Informatica e Automatica}
\courseorganizer{Facoltà di Ingegneria dell'Informazione, Informatica e Statistica}
\AcademicYear{2021/2022}
\copyyear{2022}
\advisor{Prof. Giorgio Grisetti}
\examdate{22 February 2022}
\examiner{Prof. Silvia Bonomi}
\authoremail{lucchesi.1765134@studenti.uniroma1.it}
\website{https://github.com/jcondor98/ammc}

\begin{document}

\frontmatter
\maketitle

\dedication{
Dedicated to my family, my granddad Pietro, my mom Anna Rosa, my dad Marco,
my grandmom Pierina and my sister Valentina, which I thank everyday for
everything I am.\\
To my dearest friends in Pitigliano, with whom I share some of the most
beautiful memories I have.\\
To Nicola, with whom I have shared part of this path; he helped me in a
dark period of my life and he is one of my dearest friends.
}

\import{./misc}{abstract.tex}

\tableofcontents
{
  \listoftables
  \let\cleardoublepage\clearpage
  \listoffigures
}

\mainmatter
\import{./chapters/}{01-introduction.tex}
\import{./chapters/}{02-client.tex}
\import{./chapters/}{03-master.tex}
\import{./chapters/}{04-slave.tex}
\import{./chapters/}{05-client-master-comm.tex}
\import{./chapters/}{06-master-slave-comm.tex}
\import{./chapters/}{07-conclusions.tex}

\backmatter
\cleardoublepage
\phantomsection % Give this command only if hyperref is loaded

\addcontentsline{toc}{chapter}{\bibname}
\bibliographystyle{plain}
\bibliography{main}

\end{document}

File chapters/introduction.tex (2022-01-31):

\chapter{Introduction}
\label{ch:intro}

\section{Motivation}
The use of dc motors is widespread in many application fields. Often, the
offered solutions are monolithic and use of very specific (and sometimes ad-hoc
developed) hardware. The ammc ecosystem focuses on the use of very common,
affordable and easily available hardware, such as AVR microcontrollers.

The software is designed to be modular, extensible and easily hackable by any
average C programmer, so that in the future other people interested in this
project can contribute or adapt ammc to fit their needings and accomplish their
business logic.

\section{Contributions}
The ammc ecosystem offers a flexible, affordable, hackable solution for the
management of multiple dc motors. It is composed of three main components:

\begin{itemize}
  \item A client-side application
  \item A master controller
  \item One or more slave controllers
\end{itemize}

\subsection{Client}
The client-side application is written in C. It makes use of the POSIX standard
library, and in particular the \emph{termios} interface to generic serial
devices. It offers a shell-fashioned terminal user interface.

\subsection{Master}
The master controller is an AVR microcontroller unit. The firmware is written
in C, using the \emph{avr-gcc} compiler and the \emph{avr-libc} standard
library implementation. It dispatches user commands (taken by the client) to
slave controllers.

\subsection{Slave}
The slave controllers are AVR microcontroller units. The firmware is written in
C, using the \emph{avr-gcc} compiler and the \emph{avr-libc} standard library
implementation. Each slave controller manages a single dc motor, taking
commands by the master controller.

\section{Technical approach}

\subsection{Software architecture}
I have developed all the top-level ammc components following the principles I
have learned both from my University courses\cite{fondamenti2-prog} and my
personal insights\cite{clean-architecture}\cite{cpp-ref}.

The client application and the microcontroller firmwares were developed
following the \emph{SOLID} principles, with attention on the \emph{Open-Close
principle}.  I have put particular attention on modularity; many of the
software modules found in all the ammc applications are standalone and will
work out of the box if brought into other projects.

I tried to develop my software with the following policy: the core of the
application should be composed of reusable, standalone modules; the business
logic of the application, which obviously changes radically from project to
project, should be placed in the peripheral modules and should use, when
possible, interfaces for dependency inversion towards the core modules.

For example, in the master controller firmware source code I use function
pointers to generalize the operations to be triggered by client commands.
Naturally, such practices would have been easier and more evident with a
programming language explicitly supporting the object-oriented paradigm (e.g.\
C++).

%\subsection{Coding standards}
% TODO

\subsection{Documentation}
Documentation is paramount in any software project; Damian Conway once said:
"Documentation is a love letter that you write to your future self". I did my
best to write precise and exhaustive documentation for every software piece I
realized.

This thesis is by itself a document dealing with every aspect of the ammc
project. The \texttt{README.md} file in the root directory of the repository
offers a more concise resume.

All the source code (the head files in particular) are exhaustively documented
with \emph{doxygen}, a tool which automatically converts properly formatted
comments found in the code into technical documentation; such resource is
available in the \texttt{gh-pages} git development branch and is hosted using
GitHub Pages.

The client-side application is documented with a Unix man page, which can also
be found in this thesis in section \ref{sec:client-manpage}.

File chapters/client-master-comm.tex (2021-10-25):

\chapter{Client-Master communication}
\label{ch:client-master-comm}
The client application and the master controller communicate over a protocol
built on top of the serial-over-usb layer. Such protocol is completely binary
and packet-based. Each packet has a variable length (with a total maximum size
of 36 bytes) and its integrity is checked with a trailing CRC-8 checksum.

The protocol comes with a simple handshaking mechanism, in order to synchronize
the packet IDs between endpoints and as a shallow proof of correct
functionality of the communication layers.

\section{Serial layer}
Data exchange between client and master relies on the serial protocol. For the
client application, the \emph{termios} library is used, while for the master
controller the (hardware) serial subsystem offered by the AVR
microcontroller\cite{at2560-ref} is used.

The serial communication is set up as follows:
\begin{itemize}
  \item Baud rate of 115200 baud, double speed transmission
  \item 8 bit frame width
  \item No start bits, 1 stop bit (i.e.\ 8N1)
  \item No embedded parity bit
\end{itemize}

For the master controller, both transmission and reception are
interrupt-driven, so the communication main routine is only called when data is
actually available.

\section{Packet headers}
Each packet's metadata is contained in a fixed size header, composed as
describe in table \ref{tab:packet-header}.

\begin{table}[bh]
  \begin{tabularx}{\textwidth}{c c X}
    \toprule
    Field & Size (bits) & Description \\
    \midrule
    id       & $8$ & Packet ID \\
    type     & $8$ & Packet type \\
    selector & $8$ & Selector for DC motors. Also used to store error codes in NAK packets \\
    size     & $8$ & Total packet size, including header and checksum \\
    \bottomrule
  \end{tabularx}
  \caption{Packet header fields}
  \label{tab:packet-header}
\end{table}

\subsection{Identifiers}
The \emph{id} field stores the packet identifier, which is incremental and can
be repeated in a single communication session. When the handshake is performed,
or when any endpoint raises an error (issuing a \emph{NAK} packet), the id is
reset to zero for both sides. Each \emph{ACK} and \emph{NAK} packet is
generated with the same id of the referred packet (see
\ref{client-master-comm-ackerr} for further informations).

\subsection{Packet types}
The \emph{type} field stores the packet type. An exhaustive list of packet
types is given in table \ref{tab:packet-types}

\begin{table}[bh]
  \begin{tabularx}{\textwidth}{c c X}
    \toprule
    Type & Code & Description \\
    \midrule
    \texttt{NULL}       & \texttt{0x00} & Reserved, never use \\
    \texttt{HND}        & \texttt{0x01} & Handshake \\
    \texttt{ACK}        & \texttt{0x02} & Acknowledgement \\
    \texttt{NAK}        & \texttt{0x03} & Communication error \\
    \texttt{ECHO}       & \texttt{0x04} & Echo between client and master (debug only)\\
    \texttt{TWI\_ECHO}  & \texttt{0x05} & Echo a single char to the first slave via TWI (debug only)\\
    \texttt{GET\_SPEED} & \texttt{0x06} & Get the current speed for a dc motor \\
    \texttt{SET\_SPEED} & \texttt{0x07} & Set (and apply) the speed for a dc motor \\
    \texttt{APPLY}      & \texttt{0x08} & Tell all the slaves to apply the previously set speeds \\
    \texttt{DAT}        & \texttt{0x09} & Primarily used for responses from the AVR device \\
    \texttt{SET\_ADDR}  & \texttt{0x0A} & Change the I2C address of a slave \\
    \texttt{LIMIT}      & \texttt{0x0B} & Used for sanity checks - Must have highest value \\
    \bottomrule
  \end{tabularx}
  \caption{Exhaustive list of packet types}
  \label{tab:packet-types}
\end{table}

\subsection{Motor selector}
The \emph{selector} field is used to store the identifier for the dc motor to
manipulate. This field is used in \texttt{GET\_SPEED} and \texttt{SET\_SPEED} packets.

For \emph{NAK} packets, instead, the \emph{selector} field is used to store
error codes (found in table \ref{tab:packet-error-codes}).

For all the other packet types, the \emph{selector} field is ignored.

\section{Acknowledgements and errors}
\label{client-master-comm-ackerr}
A communication endpoint must wait for an acknowledgement message from the
counterpart once it sent a packet in order to send a new one. ACK and NAK
packets do not bring any data.

When a packet arrives, it is checked for integrity and sanity. If it is sane,
then an ACK packet is sent; if not, then a NAK packet is sent.
ACK and NAK packets are simply discarded if corrupted in some way.

A NAK packet uses the \emph{selector} field to send to the other endpoint the
error code describing what happened on its side. Error codes are listed in
table \ref{tab:packet-error-codes}.

\begin{table}[bh]
  \begin{tabularx}{\textwidth}{c c X}
    \toprule
    Error & Code & Description \\
    \midrule
    \texttt{SUCCESS}             & \texttt{0x00} & No errors encountered \\
    \texttt{ID\_MISMATCH}        & \texttt{0x01} & Id of received packet is not consistent \\
    \texttt{CORRUPTED\_CHECKSUM} & \texttt{0x02} & Checksum mismatch, received packet is corrupted \\
    \texttt{WRONG\_TYPE}         & \texttt{0x03} & Received packet has invalid type \\
    \texttt{TOO\_BIG}            & \texttt{0x04} & Received packet has invalid size (too big) \\
    \bottomrule
  \end{tabularx}
  \caption{Exhaustive list of packet types}
  \label{tab:packet-error-codes}
\end{table}

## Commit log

2021-10-19 PID controller section
2021-10-20 Added schematics and wiring correspondence
2022-01-31 Updated wiring and schematics
2022-02-01 Corrected schematics and general review
2022-02-18 Complete thesis and presentation slides
    [master-schematic.kicad_sch, slave-schematic.kicad_sch]
2022-02-22 Improved schematics and added examination data
    [master-schematic.kicad_sch, slave-schematic.kicad_sch]
